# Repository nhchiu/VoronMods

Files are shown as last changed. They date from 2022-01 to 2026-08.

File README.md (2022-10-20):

# VoronMods



Collection of mods for Voron printers.

Feedbacks are welcome. @nhchiu#0363 on [Voron's Discord](https://discord.gg/voron) .

Support my work:



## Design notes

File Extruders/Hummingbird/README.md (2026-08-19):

# Hummingbird Extruder

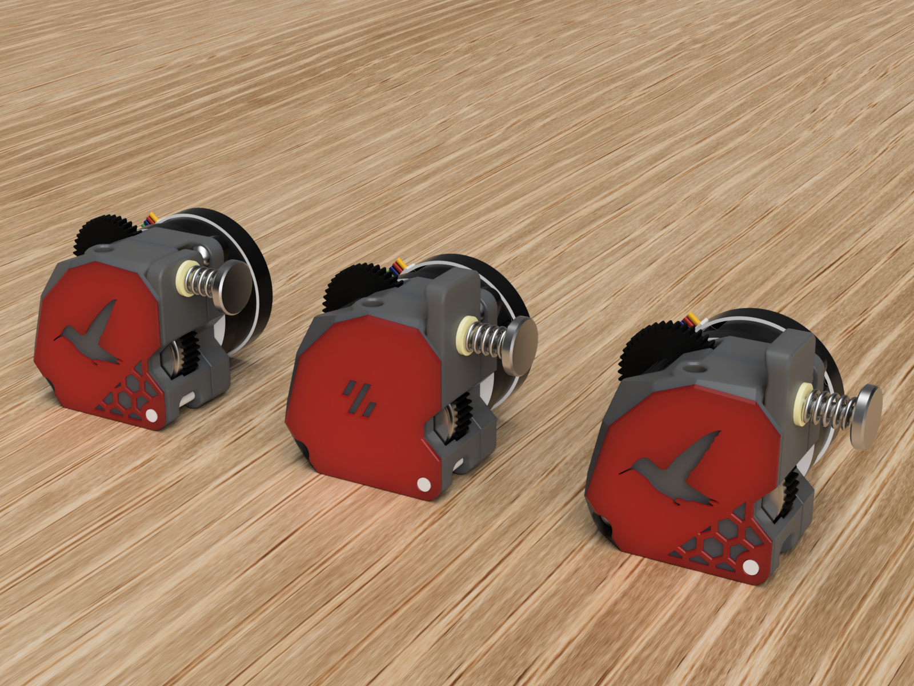
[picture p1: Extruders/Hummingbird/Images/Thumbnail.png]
Thumbnail


A compact extruder design that has the same form factor and mounting pattern as the [Bondtech LGX Lite](https://www.bondtech.se/product/lgx-lite-large-gears-extruder/).

It utilizes the large extrusion gears of [HGX-lite gear kit](https://www.aliexpress.com/item/1005004699143725.html) to accomplish high gear ratios and good filament grip.



> This page contains affiliate links. If you purchase products through these links, I may earn a small commission at no additional cost to you.
> This helps support the development and maintenance of my projects. Thank you for your support!

## BOM

- HGX Lite extruder gear kit ([AliExpress affiliate link](https://s.click.aliexpress.com/e/_DCabyeT))
  - Fasteners:
    - M3x8mm BHCS x 1
    - M3x12mm BHCS x 1
    - M3x20 SHCS x 1
    - Heat set inserts (M3 x D4.5 x H5) x 6
  - MR63ZZ bearings x 2
  - 3mm shaft (16mm length) x 2
  - 3mm shaft (24mm length) x 1
  - Large extrusion gear with pin bearing x 2
  - Reduction gear x 1
- NEMA14 36mm round pancake motor with 10T gear (Affiliate links: [Moons](https://s.click.aliexpress.com/e/_DlgBbDN) or [LDO](https://s.click.aliexpress.com/e/_Dm8FCDD))
- A short piece of PTFE tube (4mm OD, 2mm ID)

## Print Settings

Same as Voron spec. 4 perimeters, 40% infill. No support required.

To have the dual color effect as shown in the photo bellow, pause the print at 0.8mm height and change the filament color.

### Tip for bridging over the hexagonal grid

Use a height range modifier at 0.5-0.6 (mm) or add a cube modifier and place it at the height of the bridging, and force the bridging layer to print with only 2 perimeters.

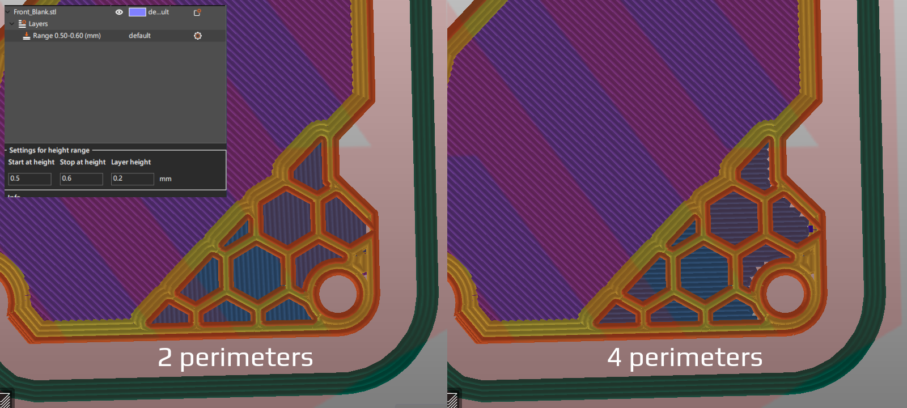
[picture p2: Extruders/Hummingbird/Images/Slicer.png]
Slicer


## Assembly

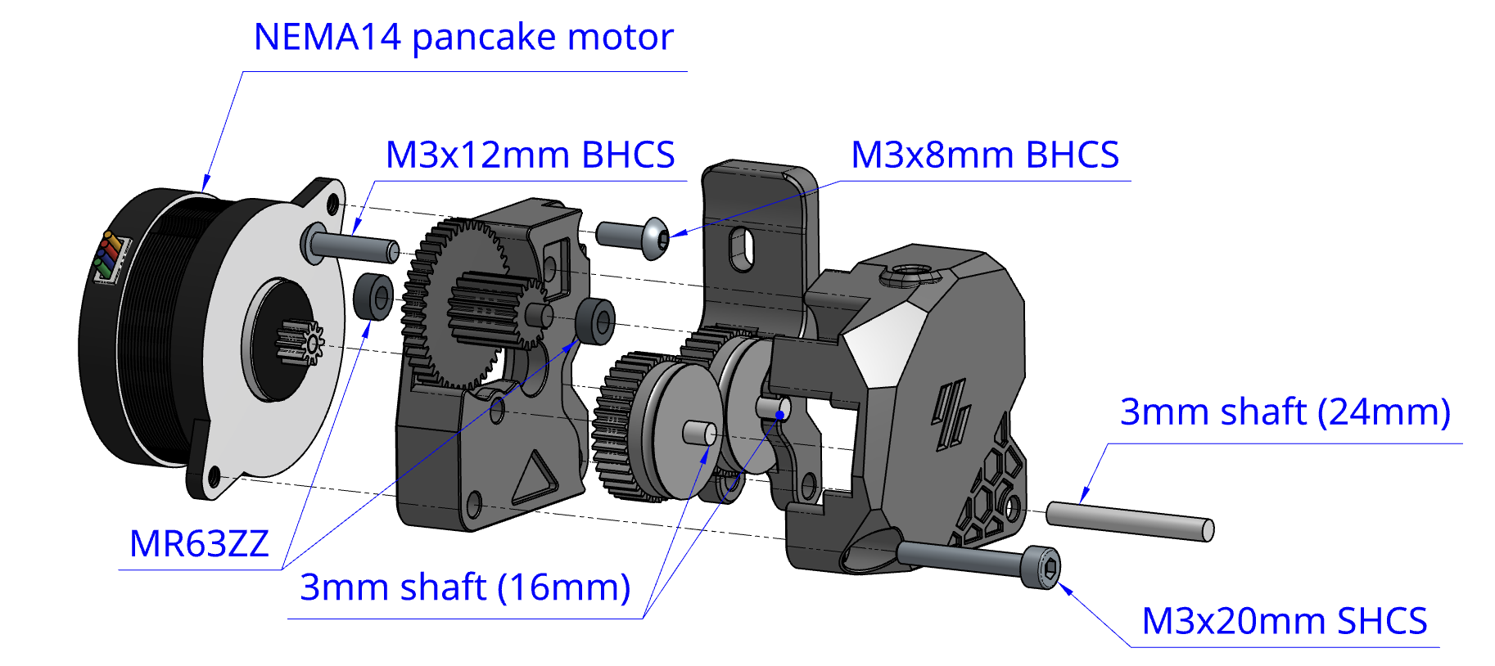
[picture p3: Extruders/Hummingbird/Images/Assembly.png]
Assembly


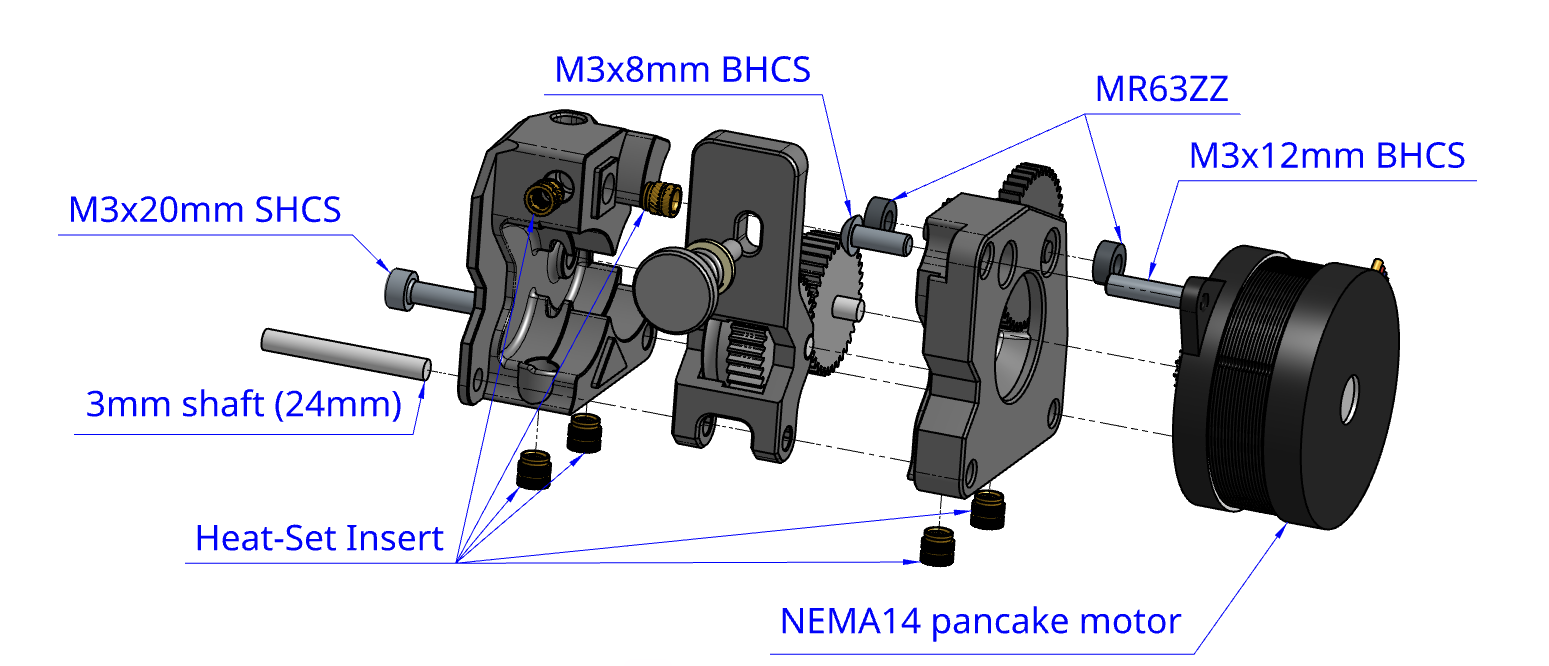
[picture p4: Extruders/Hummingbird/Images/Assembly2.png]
Assembly2


## Key Dimensions

All dimensions are in millimeters.

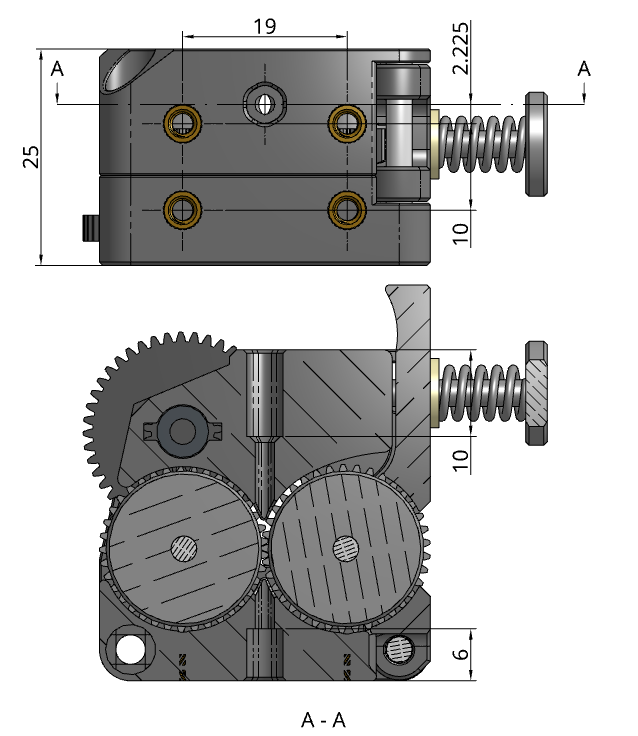
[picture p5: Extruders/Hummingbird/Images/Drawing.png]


## Firmware Settings

Only tested on [klipper firmware](https://www.klipper3d.org/):

```ini
[extruder]
rotation_distance: 53.494165  # Re-calibrate your own value
gear_ratio: 44:10, 37:17
```

## Photos

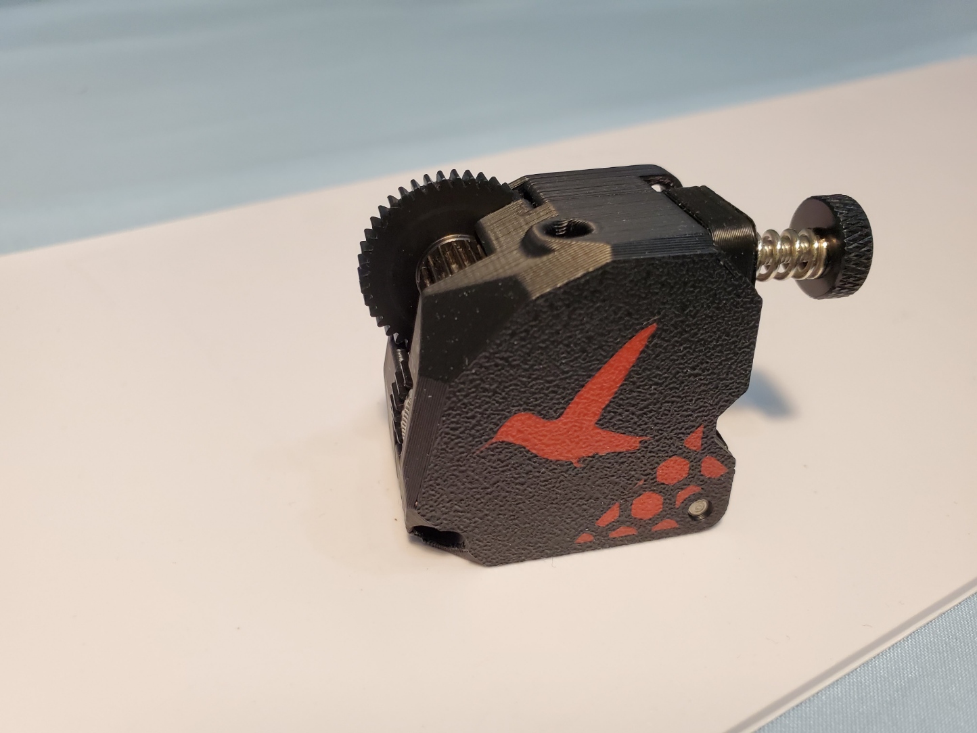
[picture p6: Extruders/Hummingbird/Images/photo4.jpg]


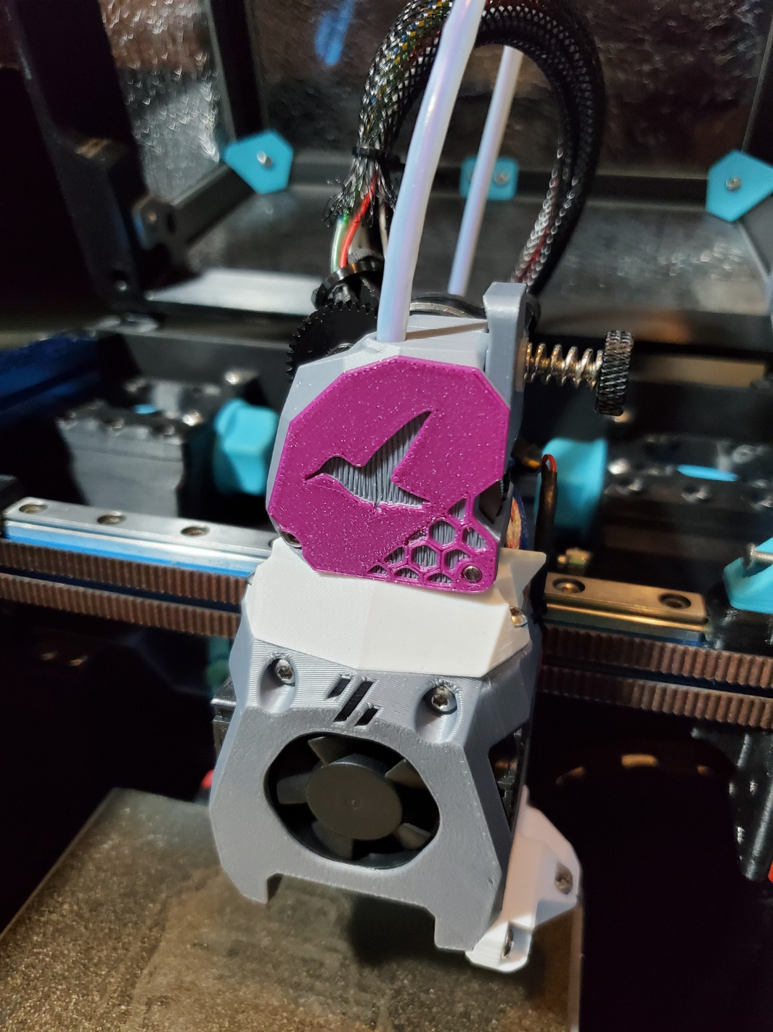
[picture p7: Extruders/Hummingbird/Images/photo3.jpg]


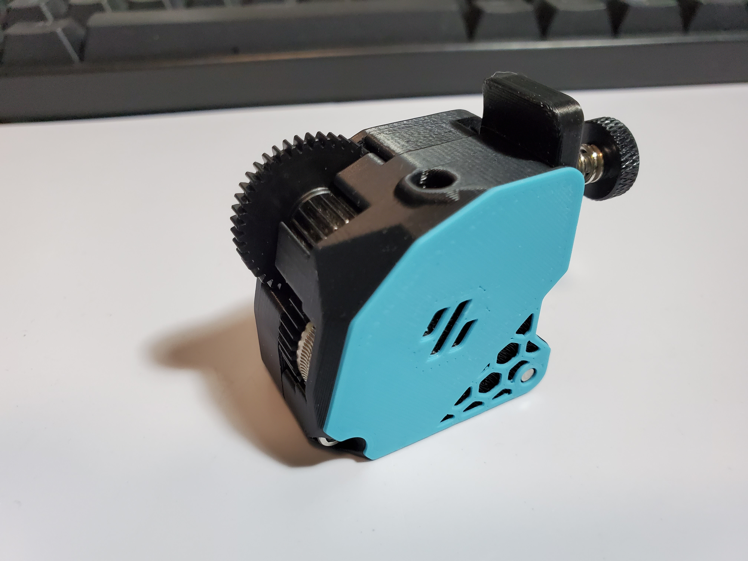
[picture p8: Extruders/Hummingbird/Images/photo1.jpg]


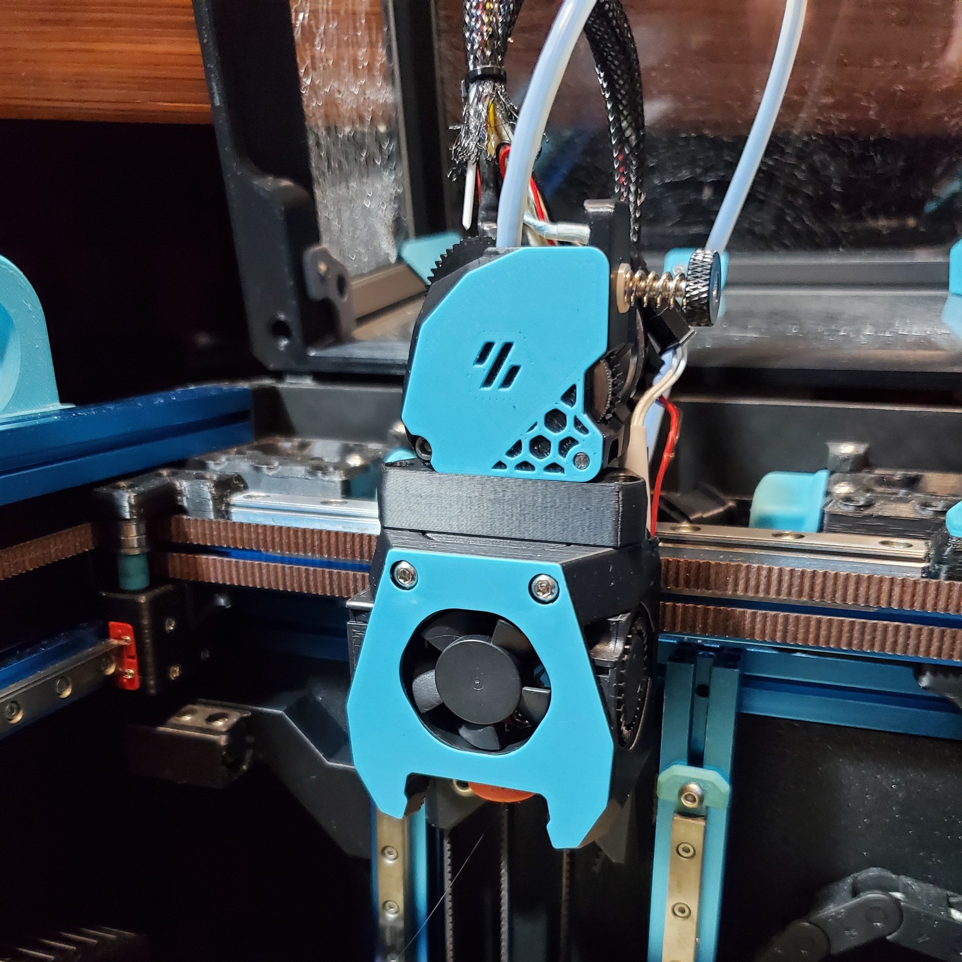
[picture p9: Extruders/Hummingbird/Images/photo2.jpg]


## Changelog

### 2024-05-08

- Removed the mockup gears in CAD to avoid confusion.

### 2023-06-28

- Added support for 3 kinds of PTFE tube retainers (4mm OD).

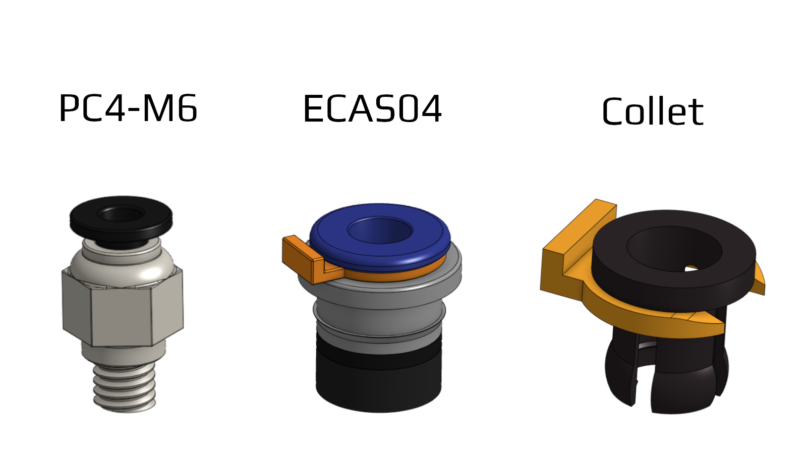
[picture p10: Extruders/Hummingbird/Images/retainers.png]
retainers
  

### 2023-05-02

- Increased the maximum distance that the idler gear can bite into the filament.
  This should prevent the filament from slipping due to the back pressure in the hotend.
- Made the idler arm thicker so it doesn't get bent over time.
- Added a multi-body STL (with MMU in the filename) for printing on a printer with MMU.

### 2023-04-01

- New hummingbird logo curtesy of #chewy2420 on Discord!
- Added a version without the hexagonal grid for easier print.
- New short idler arm for compact looking (you can still feed the filament by rotating the exposed large gear).
- Removed some plastic and tweaked some dimensions. **No part is compatible with previous versions!**

### 2023-01-13

- Initial release

## Credits and Related Projects

- [Bondtech LGX Lite - Large Gears eXtruder](https://www.bondtech.se/product/lgx-lite-large-gears-extruder/)
- [LGX lite Extruder on Printables](https://www.printables.com/model/282297-lgx-lite-extruder-fdm-case/comments) by [SIVIS](https://www.printables.com/social/263178-sivis)
- **Pixel Printing** on Discord for the name of the extruder

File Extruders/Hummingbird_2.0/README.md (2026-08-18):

# Hummingbird Extruder 2.0

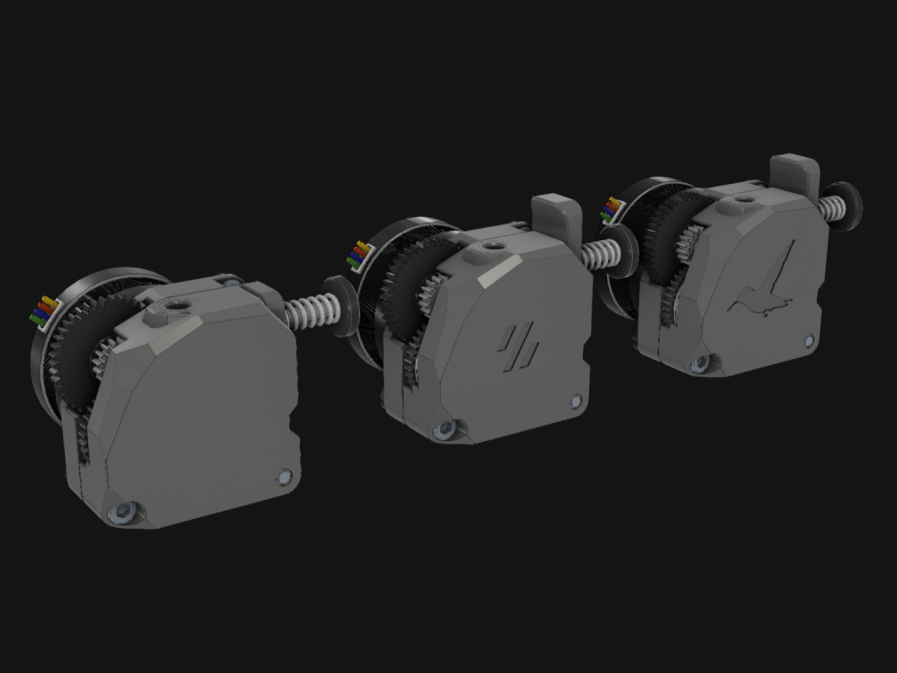
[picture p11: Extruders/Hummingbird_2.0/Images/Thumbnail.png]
Thumbnail


A compact extruder design that has the same form factor and mounting pattern as the [Bondtech LGX Lite](https://www.bondtech.se/product/lgx-lite-large-gears-extruder/).

Although it is named Hummingbird **2.0**, it's not a direct upgrade from the previous design.
There's not much you can reuse in the BOM.

It utilizes the large extrusion gears of [HGX-lite **2.0** Extruder](https://s.click.aliexpress.com/e/_Dmy9Crl) **(affiliate link)** to accomplish high gear ratios and good filament grip.

If you would like to support my work, the following platforms are available. Thank you!




> This page contains affiliate links. If you purchase products through these links, I may earn a small commission at no additional cost to you.
> This helps support the development and maintenance of my projects. Thank you for your support!



## BOM

- HGX Lite **2.0** extruder gear kit ([This](https://s.click.aliexpress.com/e/_Dmy9Crl) or [this](https://s.click.aliexpress.com/e/_Dn3gb6n)) **(Both are affiliate links)**.
  - MR63ZZ bearings x 6
  - 3mm shaft (16mm length) x 1
  - 3mm shaft (13mm length) x 1
  - Large extrusion gear x 2
  - Reduction gear x 1
- Fasteners:
  - M3x8mm BHCS x 1
  - M3x12mm BHCS x 1
  - M3x20 SHCS x 2
  - Heat set inserts (M3 x D5 x H4) x 4
- NEMA14 36mm round pancake motor with 10T gear
- A short piece of PTFE tube (4mm OD, 2mm ID)

## Print Settings

Same as Voron spec. 4 perimeters, 40% infill. No support required.

To have the dual color effect as shown in the photo bellow, pause the print at 0.8mm height and change the filament color.

## Assembly

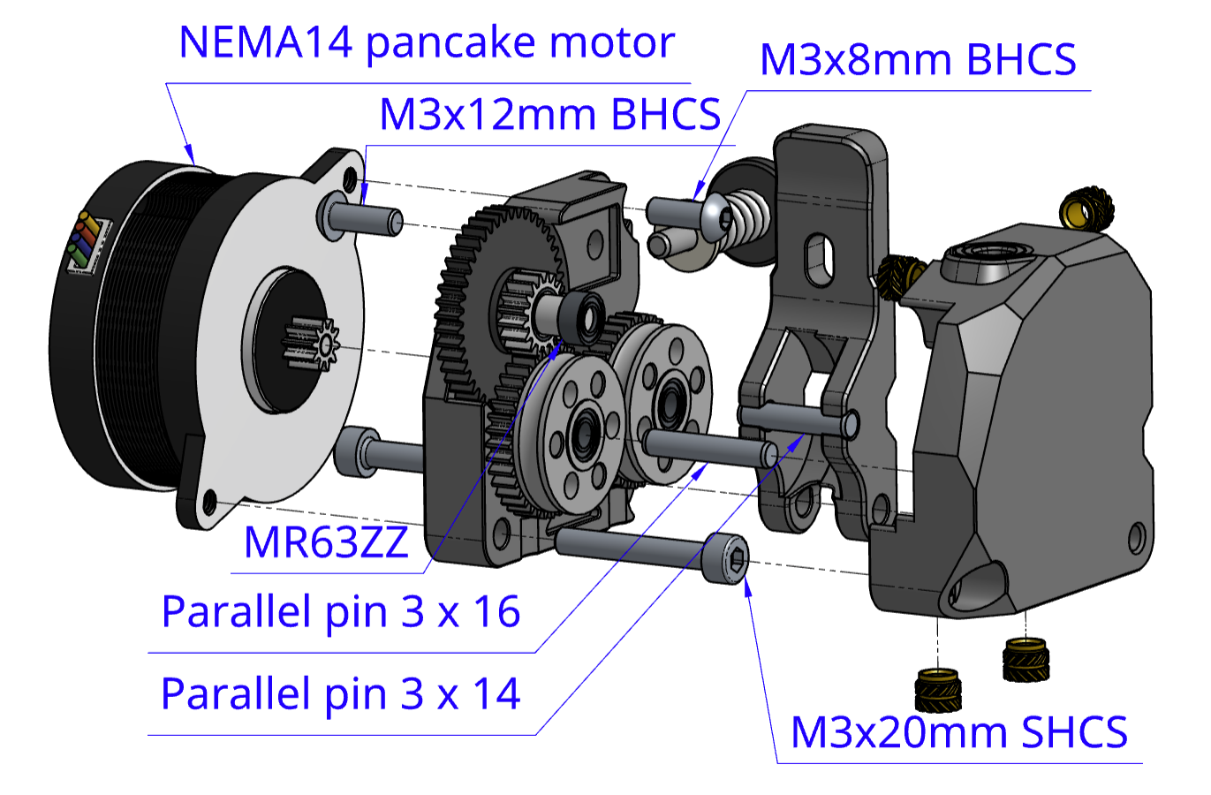
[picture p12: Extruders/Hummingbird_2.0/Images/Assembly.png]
Assembly


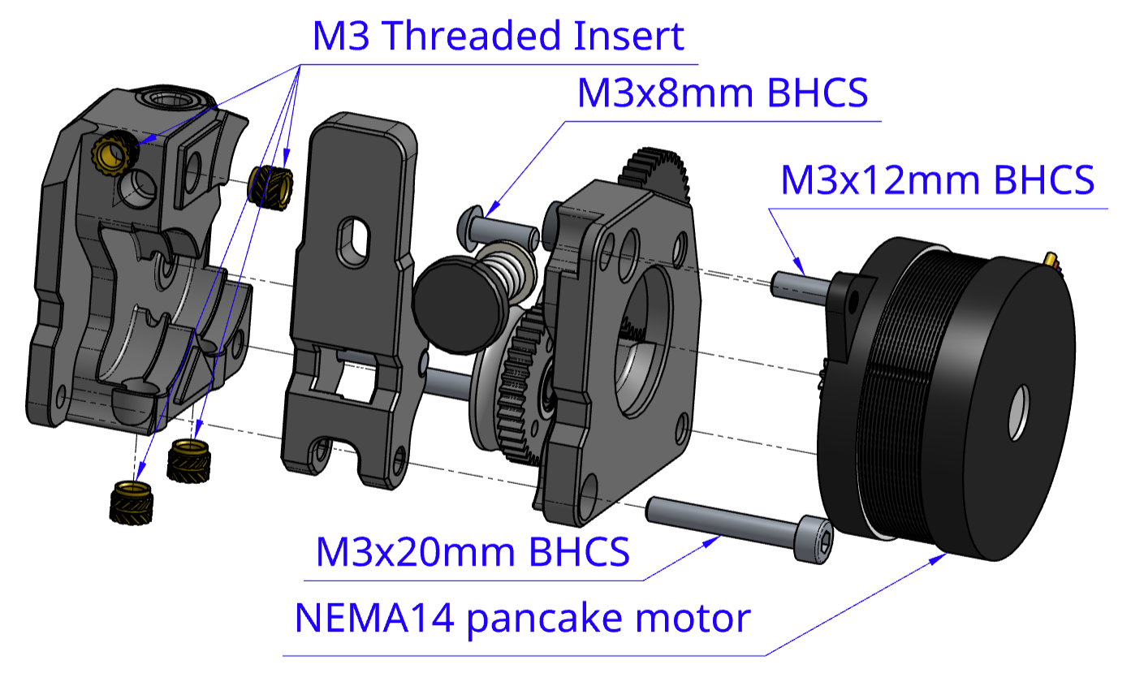
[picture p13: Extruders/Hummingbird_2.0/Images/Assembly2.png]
Assembly2


## Key Dimensions

All dimensions are in millimeters.

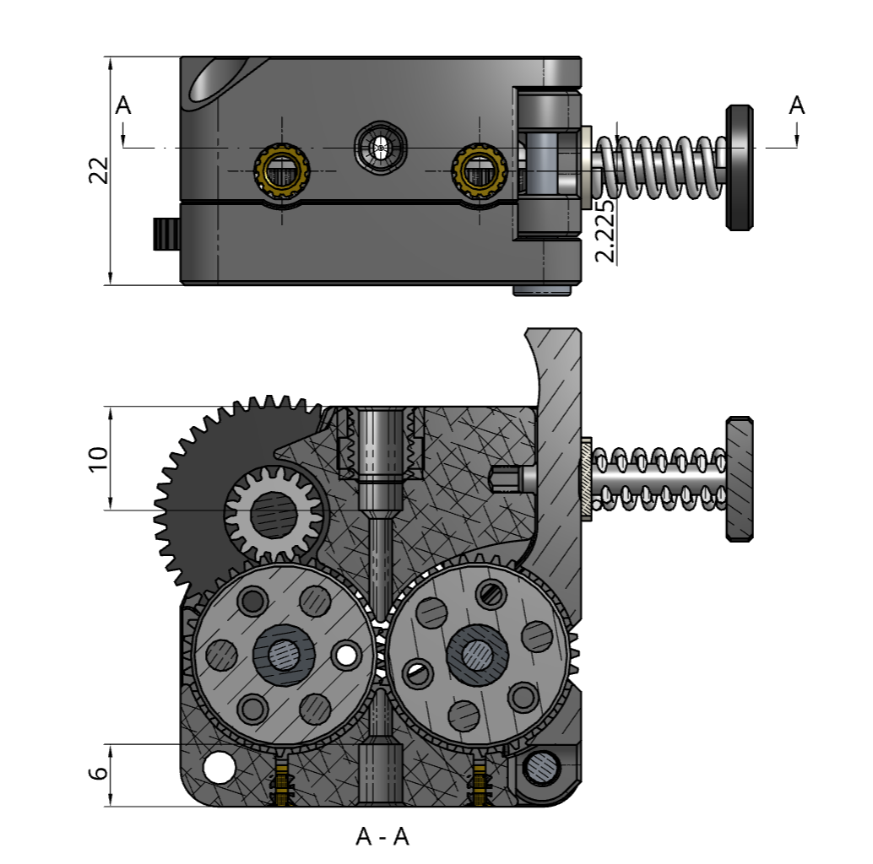
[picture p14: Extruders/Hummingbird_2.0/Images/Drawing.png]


## Firmware Settings

Only tested on [klipper firmware](https://www.klipper3d.org/):

```ini
[extruder]
rotation_distance: 53.494165  # Re-calibrate your own value
gear_ratio: 44:10, 37:17
```

## Photos

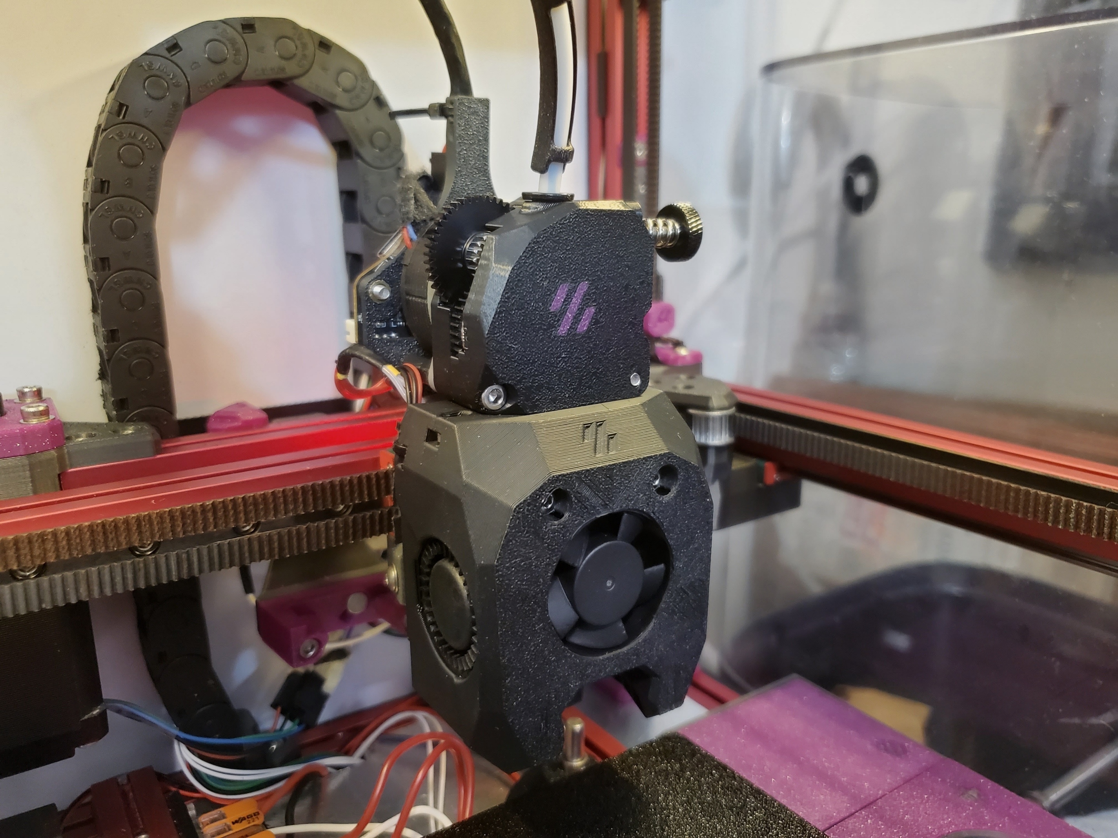
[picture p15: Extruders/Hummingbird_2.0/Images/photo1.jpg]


## Changelog

### 2026-08-18

- Initial release

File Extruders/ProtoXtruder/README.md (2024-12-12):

# ProtoXtruder

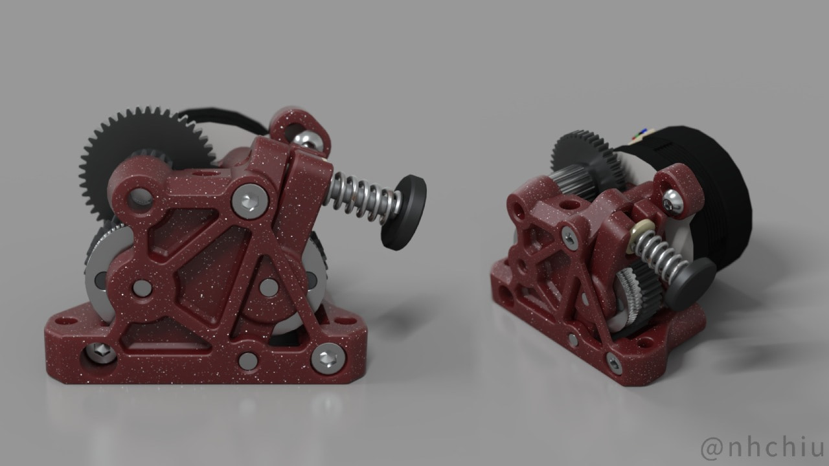
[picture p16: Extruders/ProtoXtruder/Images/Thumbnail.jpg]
Thumbnail


A extruder design that utilizes the large extrusion gears of [HGX-lite gear kit](https://www.aliexpress.com/item/1005004699143725.html)
and comes with the mounting pattern of the [Sherpa Mini Extruder](https://github.com/Annex-Engineering/Sherpa_Mini-Extruder).

There is also an **untested** version for [Bondtech LGX Lite](https://www.bondtech.se/product/lgx-lite-large-gears-extruder/) gears.

Refer to the following dimensions for compatibility with your printer.

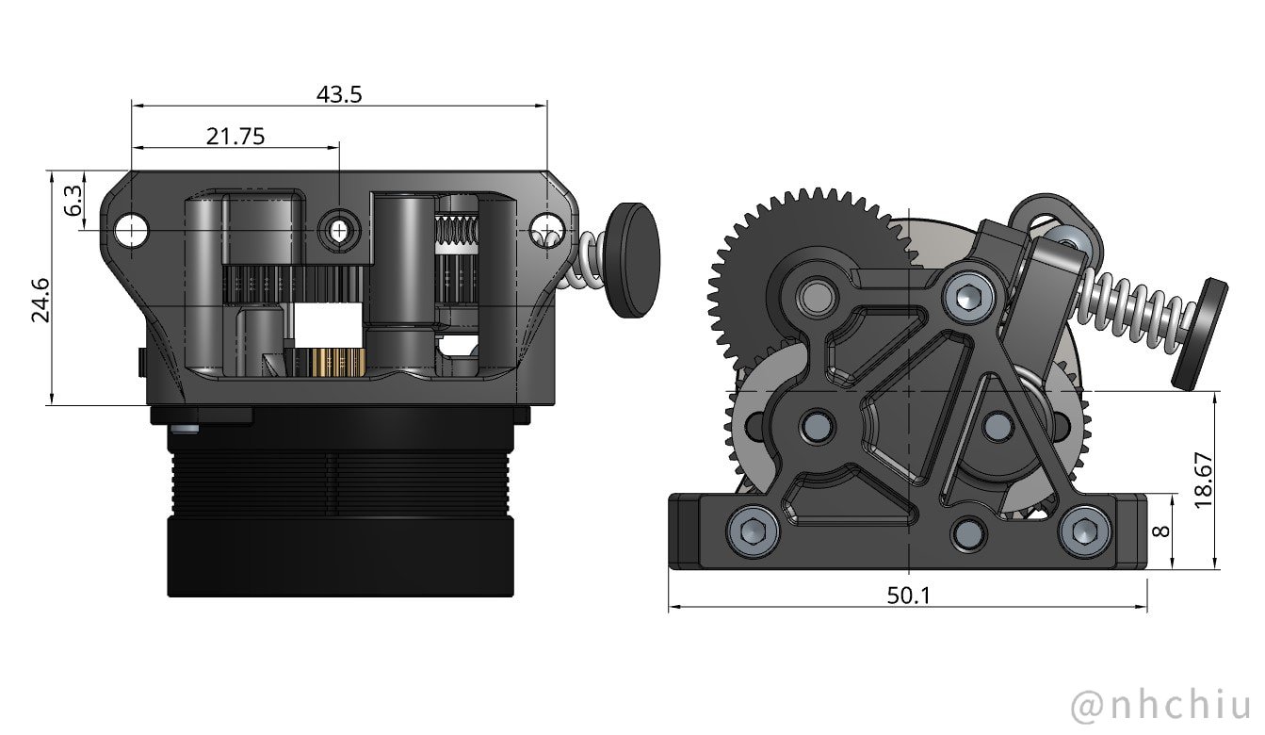
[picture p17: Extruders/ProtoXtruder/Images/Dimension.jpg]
Dimension




> This page contains affiliate links. If you purchase products through these links, I may earn a small commission at no additional cost to you.
> This helps support the development and maintenance of my projects. Thank you for your support!

## BOM

- HGX Lite extruder gear kit ([AliExpress affiliate link](https://s.click.aliexpress.com/e/_DCabyeT))
  ***Newer kits replaced each pin bearing with 2 MR63ZZ. Both versions will work. (But the gears have different ID so they are not interchangeable.)***
  - MR63ZZ bearings x 2
  - 3mm shaft (16mm length) x 2
  - 3mm shaft (24mm length) x 1
  - Large extrusion gear with pin bearing x 2
  - Reduction gear x 1
  - Fasteners (included in the gear kit):
    - M3x8mm BHCS x 1
    - M3x20mm SHCS x 3
    - Heat set inserts (M3 x D4.5 x H5) x 3
- NEMA14 36mm round pancake motor with 8T or 10T gear (Affiliate links: [Moons](https://s.click.aliexpress.com/e/_DlgBbDN) or [LDO](https://s.click.aliexpress.com/e/_Dm8FCDD))

## Print Settings

3 perimeters, 40% infill. ABS recommended.

All STLs are oriented in the printing orientation. No support required.

It will need some bridging.

## Assembly

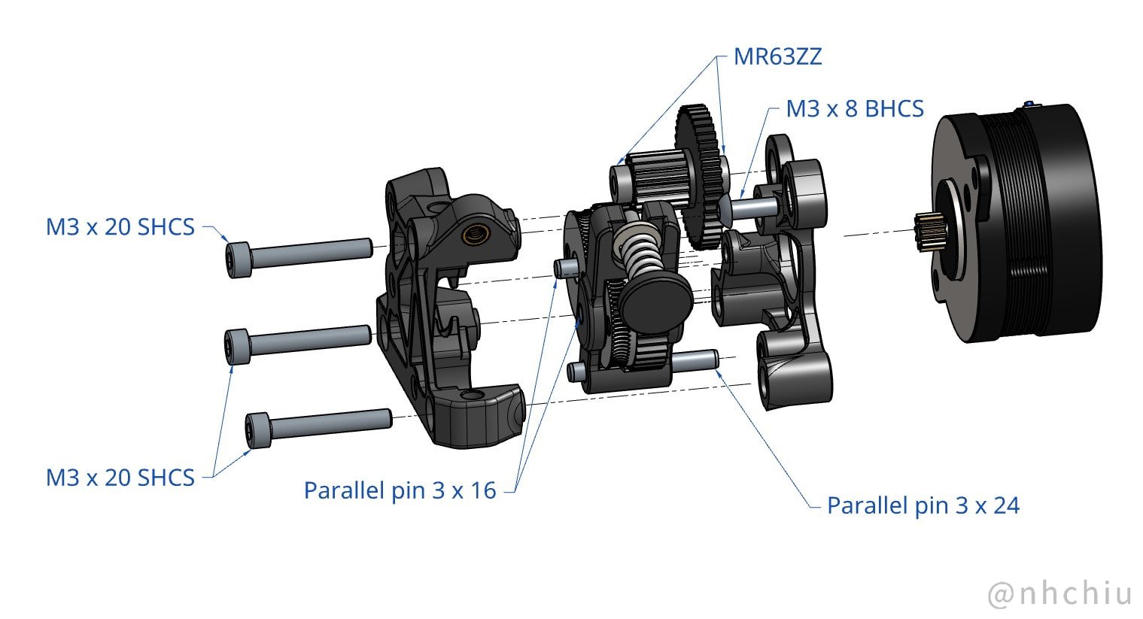
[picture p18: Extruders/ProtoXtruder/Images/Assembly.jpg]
Assembly


\* Remove the bottom half of the ECAS04 before inserting. (the black parts in plastic/rubber)

https://user-images.githubusercontent.com/14959712/228478235-7f9f1ea8-db8a-41ff-84bd-ff1c1cee3275.mp4

## Firmware Settings

For [klipper firmware](https://www.klipper3d.org/):

```ini
[extruder]
rotation_distance: 53.494165  # Re-calibrate your own value
gear_ratio: 44:10, 37:17
```

**You have to invert the `dir_pin` of the extruder if you were using a BMG gear kit.**

## Photo

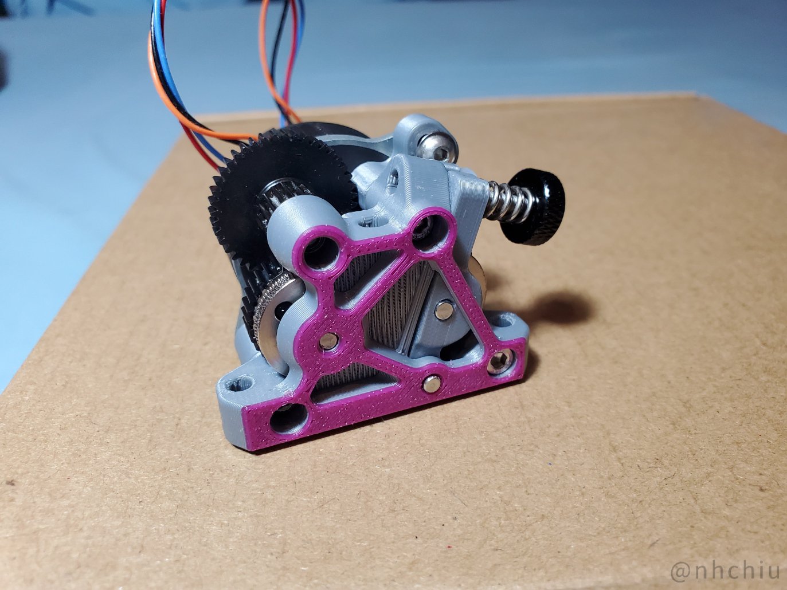
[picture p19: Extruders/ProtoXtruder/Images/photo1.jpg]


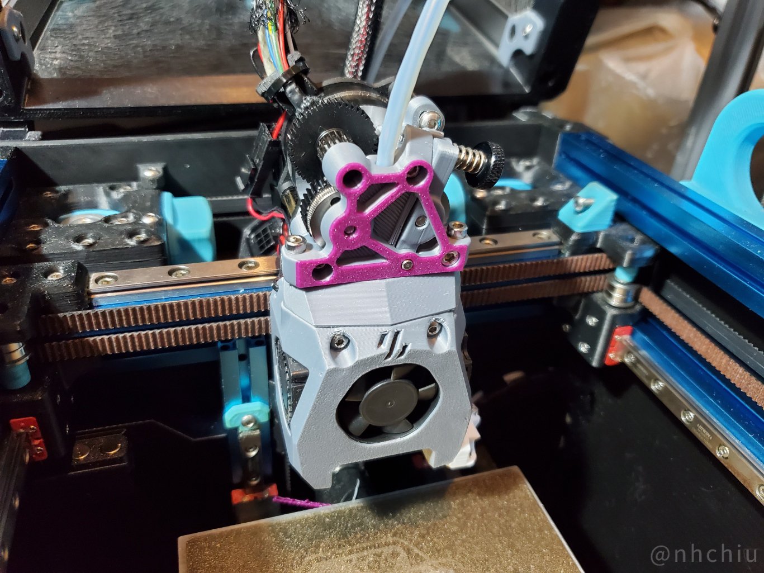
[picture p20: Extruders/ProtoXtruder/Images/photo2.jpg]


## Changelog

### 2024-12-12

Bugfix update.

- Thicker idler arm to prevent it being bent over time. Hopefully fixes [#20](https://github.com/nhchiu/VoronMods/issues/20).
- The update at 2024-08-01 might cause the idler arm being bottomed out by tension and
  still not providing enough pressure on the filament. Slightly shortened the distance between the
  dual drive gears to address this issue.

### 2024-10-21

- Updated the collet cutout for better tube retaining and filament loading.
  No changes were made to other variants.
  Thanks to @MartijnGevaert for the suggestion.

### 2024-08-01

- Made better measurements of the HGX gears and slightly tweaked some dimensions accordingly.
- Some overall cleanups and aesthetic adjustments. Now the printed parts use roughly 10% less plastic.

### 2023-07-02

- Increase the maximum compression on the filament for better gripping.
- Fix the hole size of the idler shaft so it doesn't slip out during print.
- Variants for 3 types of Bowden tube retainers.

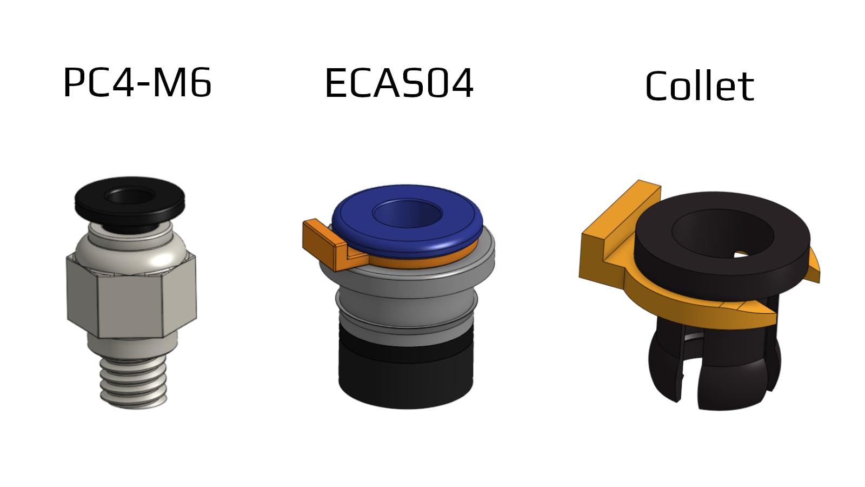
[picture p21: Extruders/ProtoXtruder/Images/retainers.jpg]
retainers
  
- Replaced the M3 x 16 screw to M3 x 20 to make space for the Bowden tube retainers.

### 2023-03-29

- Initial release

## Credits

- [Sherpa Mini Extruder](https://github.com/Annex-Engineering/Sherpa_Mini-Extruder) by [Annex Engineering](https://github.com/Annex-Engineering)

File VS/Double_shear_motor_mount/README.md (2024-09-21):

# Voron Switchwire Double Shear Motor Mount

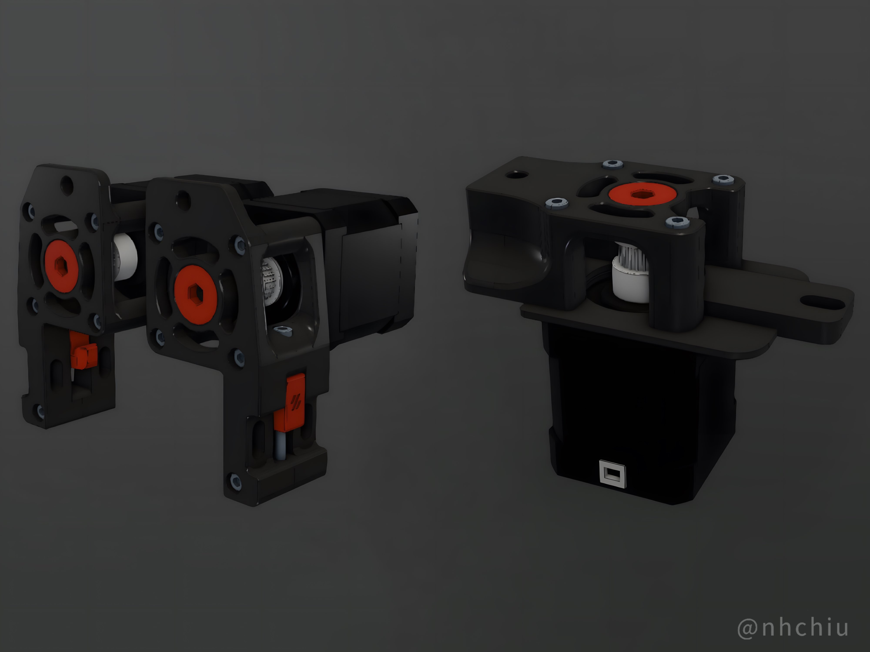
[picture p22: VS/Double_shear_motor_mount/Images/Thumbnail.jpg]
Thumbnail




This mod adds another bearing on the motor mount to support the other end of the motor shaft.
It reduces the bending effect on the shaft caused by the tension of the timing belt.
In theory it can make the motor runs smoother under high belt tension and most likely increase its lifespan too.

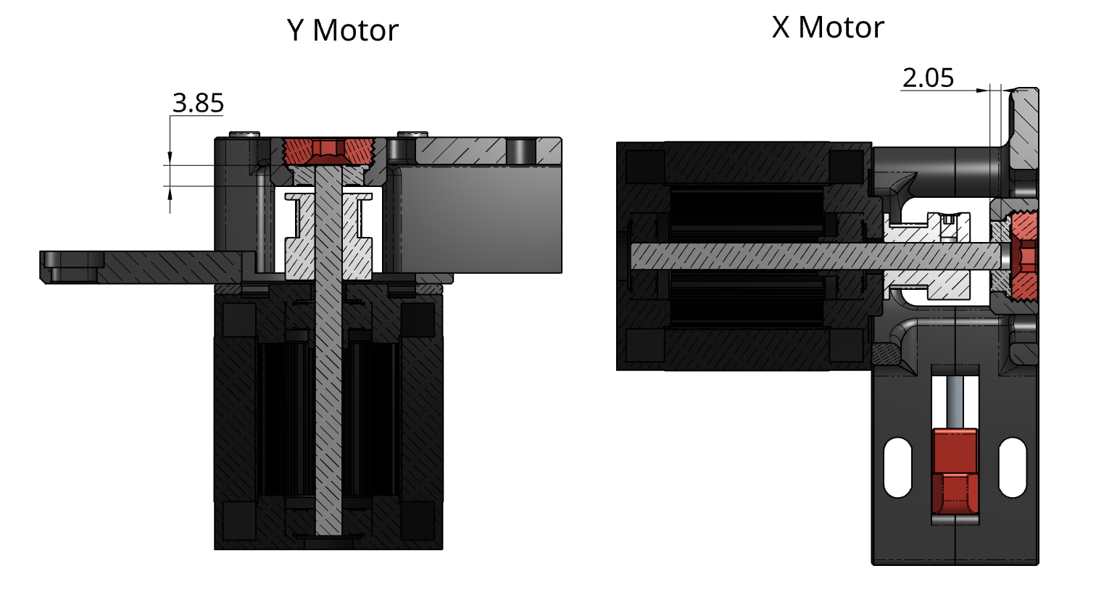
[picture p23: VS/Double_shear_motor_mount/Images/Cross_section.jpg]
cross_section


**All dimensions are designed to fit the stock Switchwire motors (24mm long shaft). If your motor has longer or shorter shaft, please check if it fits before proceeding.**
With the stock motor shaft length, the shaft can't reach through the full height of the bearing on X/Z motor mounts. But it should more or less still be helpful to hold the floating end of the shaft.

If you like my design, please consider supporting my work through the following platforms. Thank you!




## Features

- Double shear mount.
- Added indexing features between mating parts.
- Some tweaks on the XZ motor mounts ported from [SW More Robust XZ Belt Paths by yenda](https://github.com/VoronDesign/VoronUsers/tree/main/printer_mods/yenda/vsw_more_robust_belt_paths):
  - Added an additional screw at the bottom. The two halves of the motor mount tend to slightly split up and show a gap there so this screw helps holding them together.
  - An additional screw hole to help fixing the motor mount to the Z(vertical) extrusion. **Use this screw with care. Don't rely on this screw to force the motor mount to fit to the vertical extrusion. Make sure the frame is square and the motor mount is properly installed first, then install this screw lightly just as an extra reinforcement.**

    > Quote from yenda's mod:
    >
    > It has been noticed by people helping within Voron community with Switchwire builds on regular basis,
    > that the uppermost screw supposed to fix the stepper mounts to the vertical extrusions might actually cause issues if the frame is not perfectly square.
    > Please make sure your printer has its frame fully square and proceed at your discretion -- use of the uppermost screw is solely optional in any case. (Credits for this observation go to Hymness1 on Voron Discord).

## BOM

Only additional parts from the stock Switchwire design are listed here.

- X/Z motor mount (per side)
  - F695 bearing x 1 (either ZZ or RS type would work)
  - M3xD5xH4 threaded insert x 1
  - M3x25 SHCS x 1
  - M5x10 BHCS x 1 and M5 T-nut for 3030 extrusions x 1 (Optional. For attaching to the Z extrusion)
- Y motor mount
  - F695 bearing x 1 (either ZZ or RS type would work)
- Extra tools
  - 5mm Allen key / hex driver (Just for tightening the bearing retainer. Printed hex key might work too.)

## Print Settings

Same as Voron spec. 0.2mm layer height, 4 perimeters, 40% infill, 5 solid top/bottom layers.

All STLs are oriented in the printing orientation. No support required.

## Assembly

Please refer to [Assembly_Manual.pdf](./Assembly_Manual.pdf).

## Photos

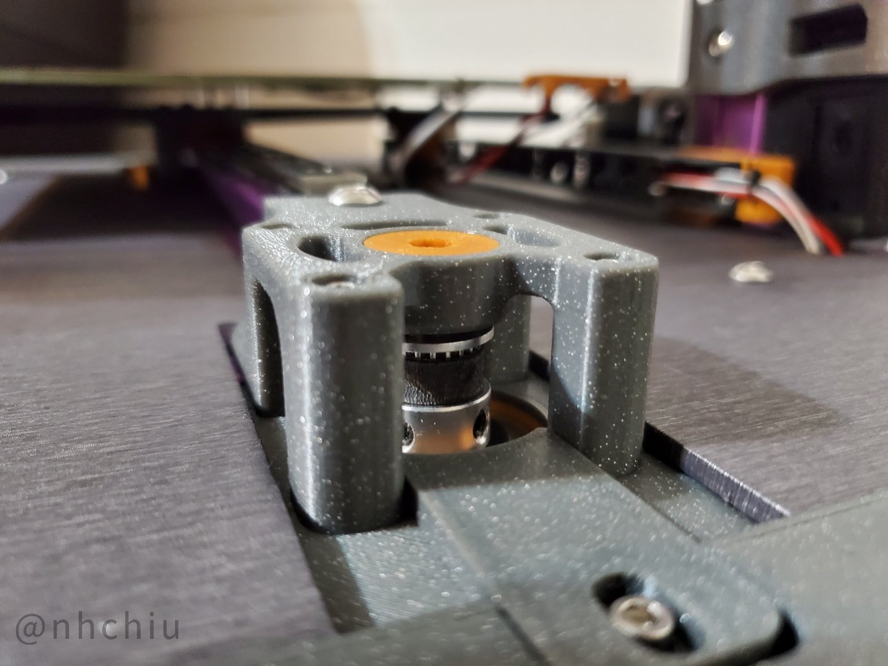
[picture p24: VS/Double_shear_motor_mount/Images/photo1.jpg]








## Changelog

### 2024-09-21

- Initial release

## Credits

- [Voron Switchwire](https://github.com/VoronDesign/Voron-Switchwire)
- [SW More Robust XZ Belt Paths by yenda](https://github.com/VoronDesign/VoronUsers/tree/main/printer_mods/yenda/vsw_more_robust_belt_paths)

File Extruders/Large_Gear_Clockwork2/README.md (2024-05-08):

# Large Gear Clockwork2

Thumbnail

As title, it's basically [Voron Clockwork2](https://github.com/VoronDesign/Voron-Stealthburner/tree/main/STLs/Clockwork2) utilizing the large extrusion gears of [HGX-lite gear kit](https://www.aliexpress.com/item/1005004699143725.html) or [Bondtech LGX Lite eXtruder](https://www.bondtech.se/product/lgx-lite-large-gears-extruder/) to accomplish high gear ratios and good filament grip.

**If you are going to use a toolhead board, this would probably be only compatible with the 2-piece version of the [Stealthburner toolhead board](https://github.com/VoronDesign/Voron-Hardware/tree/master/Stealthburner_Toolhead_PCB) (mount it directly without the PCB spacer). The standard version will interfere with the gear below. *Check your own toolhead board / CAN board before use!***



## BOM

- HGX Lite extruder gear kit ([https://www.aliexpress.com/item/1005004699143725.html](https://www.aliexpress.com/item/1005004699143725.html))
  - MR63ZZ bearings x 2
  - 3mm shaft (16mm length) x 2
  - 3mm shaft (24mm length) x 1
  - Large extrusion gear with pin bearing x 2
  - Reduction gear x 1
- NEMA14 36mm round pancake motor with 10T gear
- Fasteners:
  - M2x10 self-tapping screw x 1
  - M3x6  BHCS x 1
  - M3x8  SHCS x 2
  - M3x16 SHCS x 1
  - M3x20 SHCS x 1
  - M3x25 SHCS x 4
  - M3xD5xH4 threaded inserts x 13 or 14 (depending on the mounting holes of your drag chain)

**Note: Use the threaded inserts in the Voron BOM. The inserts included in the HGX Lite gear kit has a different dimension!**

## Print Settings

Same as Voron spec. 4 perimeters, 40% infill.

All STLs are oriented in the printing orientation. No support required.

## Assembly

Please refer to [Assembly.pdf](./Assembly.pdf).

## Firmware Settings

For [klipper firmware](https://www.klipper3d.org/):

```ini
[extruder]
rotation_distance: 53.494165  # Re-calibrate your own value
gear_ratio: 44:10, 37:17
```

**You have to invert the `dir_pin` of the extruder if you were using a BMG gear kit.**

## Photo









## Changelog

### 2024-05-08

- Removed the mockup gears in CAD to avoid confusion.

### 2023-07-10

- Increased the maximum squish on the filament.
- Tweaked some dimensions here and there.
- Included a variant using LGX-lite gears.

### 2023-02-20

- Initial release

## Credits

- [Voron Stealthburner and Clockwork2](https://github.com/VoronDesign/Voron-Stealthburner)
- [Bondtech LGX Lite eXtruder](https://www.bondtech.se/product/lgx-lite-large-gears-extruder/)

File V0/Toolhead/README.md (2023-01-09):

# Mini Stealthdort

Thumbnail

Yet another versatile toolhead design for Voron-0.

## Features

- Shorter distance between the extruder and the hotend.
- Light-weight printed parts.
- The extruder will be mounted 4mm lower, so the tube is less likely to rub on the top-hat.
- Built in cut-out for [Klicky probe](https://github.com/jlas1/Klicky-Probe/tree/main/Printers/Voron/v0) and [ZeroClick](https://github.com/zruncho3d/ZeroClick) (use the provided probe STLs in this repo).
- Redesigned part cooling fan duct.
- Similar mounting style as [Mini AfterSherpa](https://github.com/PrintersForAnts/Mini-AfterSherpa)
  The mounting holes and dimensions are mostly compatible with Mini AfterSherpa but the top surface is 4mm lower

  

## BOM

- M3 Heatset insert x 2 (for the extruder mount)
- **M3x30mm** x 2 (for mounting to the carriage)
- 3010 blower fans for part cooling
- 3007 or 3010 axial fan for hotend cooling (depending on the hotend)

Optional:

- One M3 heatset insert for klicky probe mount
- M2x8mm screw for ZeroClick (Or use the M2 self-tapping screw with Voron BOM and trim down 2mm)
- M3x40mm x 2 (for mounting ADXL345)

## Supported Hardware

Choose the supported extruder and hotend listed bellow and print the corresponding STL files.

### Extruder

extruder

| Extruder | Printed parts |
| --- | --- |
| [Vorxtrudort](https://github.com/nhchiu/VoronMods/tree/main/Extruder) | `Cowling.stl` |
| [Sherpa Mini](https://github.com/Annex-Engineering/Sherpa_Mini-Extruder) | `Cowling.stl` |
| [Sherpa Micro](https://github.com/Annex-Engineering/Sherpa_Micro-Extruder) | `Cowling.stl` and `Sherpa_micro_adapter.stl`  |
| [Sailfin](https://github.com/CroXY3D/Sailfin-Extruder) or [Sharkfin](https://github.com/KayosMaker/Sailfin-Extruder/tree/main/Usermods/KayosMaker/Sharkfin) (with Sherpa mount variant) | `Cowling.stl` and `Sailfin_spacer.stl` |
| [Orbiter V1.5](https://orbiterprojects.com/orbiter-1-5) | `Cowling.stl` and `Orbiter_V1.5_adapter.stl`  |
| [Orbiter V2.0](https://orbiterprojects.com/orbiter-v2-0/) | `Orbiter_V2_cowling.stl` |
| [LGX Lite](https://www.bondtech.se/product/lgx-lite-large-gears-extruder/) | `Cowling.stl` and `LGX_Lite_adapter.stl` |
| [Vz-Hextrudort](https://github.com/VzBoT3D/Vz-HextrudORT) | `Cowling.stl` and `Vz-Hextrudort_adapter.stl` |

### Hotend

hotend

| Hotend | Supported Hotend Fan | Printed Part |
| --- | --- | --- |
| Phaetus Dragon | 3007 | `Dragon-Mount.stl` |
| Phaetus Dragonfly BMO | 3007 | `Dragonfly-BMO-Mount.stl` |
| Slice Engineering Mosquito | 3010 & 3007 | `Mosquito-Mount.stl` |
| E3D Revo Voron | 3010 & 3007 | `Revo-Voron-Mount.stl` |
| Mellow NF-Zone | 3010 & 3007 | `NF-Zone-Mount.stl` |

## Assembly

assembly

## ADXL345 Mount

Print out `ADXL345_Mount.stl` and mount the ADXL345 module to it with 2 M2 self-tapping screws and 2 [printed washer (from Stealthburner)](https://github.com/VoronDesign/Voron-Stealthburner/blob/main/STLs/Stealthburner/ADXL345_Mounts/sb_adxl_washer_x2.stl).

Use 2 M3x40mm screws to mount it on the toolhead for calibrating input shaper.

ADXL

## Photo



## Changelog

### 2023-01-09

- Added supported extruder: Sherpa Micro, Orbiter V2.0, LGX Lite, Vz-Hextrudort
- Added supported hotend: Mellow NF-Zone
- Modular design for hotend and extruder so switching hotend is much easier
- Tweaked the low-poly design
- Filled up the gap between the klicky probe mount and the heatset insert

### 2022-08-04

- Added untested support for Sailfin / Sharkfin extruder and Orbiter V1.5

### 2022-07-30

- Revised the fan duct
- Moved the zip tie slot higher so it clears the X carriage
- Tweaked some faces and removed most of the fillets

### 2022-07-16

- Added E3D Revo Voron support (not tested yet)

### 2022-07-10

- Initial release

## Credits and Related Projects

- [Voron-0 and Mini AfterBurner](https://github.com/VoronDesign/Voron-0) by VoronDesign
- [Mini AfterSherpa](https://github.com/PrintersForAnts/Mini-AfterSherpa)
- [Mini After-LGX-Lite](https://github.com/VoronDesign/VoronUsers/tree/master/printer_mods/Bondtech/Mini-After-LGX-Lite)
- [MiniAfterHybrid](https://github.com/camerony/VoronCustom/tree/main/v0.1_MiniAfterHybrid)
- [Apogee Tool Head](https://orbiterprojects.com/ender-3-v2/)
- [Sherpa Mini Extruder](https://github.com/Annex-Engineering/Sherpa_Mini-Extruder)
- [Sailfin Extruder](https://github.com/CroXY3D/Sailfin-Extruder)
- [Sharkfin Extruder](https://github.com/KayosMaker/Sailfin-Extruder/tree/main/Usermods/KayosMaker/Sharkfin)
- [Orbiter Projects](https://orbiterprojects.com)
- [Klicky Probe](https://github.com/jlas1/Klicky-Probe)
- [ZeroClick](https://github.com/zruncho3d/ZeroClick)

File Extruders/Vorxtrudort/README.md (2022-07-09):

# Vorxtrudort (HextrudORT for Voron)

Thumbnail

Design is based on the compact and lightweight [HextrudORT](https://miragec79.github.io/HextrudORT/).

HextrudORT is designed to be integrated with the X carriage and the hotend to make a compact toolhead, which is not directly compatable with modular toolhead design.

The major changes of Vorxtrudort are:

1. Stand-alone extruder with different mounting options.
2. Reduce printing support material.
3. Use heatset inserts instead of hex nuts.

I don't have a scale. If anyone would like to do a weight comparison with other extruder, please share it on Voron Discord.

## BOM

- Bondtech BMG internals
- NEMA14 36mm round pancake motor with 10T gear
- A short peice of PTFE tube (4mm OD, 2mm ID)
- M3 Heatset insearts (M3xD5xH4) x 4
- M3 BHCS or SHCS:
  - 8mm x 5
  - 16mm x 1
  - 20mm x 1
  - 25mm x 1
- M2 x 10mm Self Tapping Screw x 1

## Print Settings

Same as Voron spec. 4 perimeters, 40% infill.

No support. There are built-in support in the STL.

## File Naming

There are several variations. For the coresponding files they are named as follows:

`Part_Name_[Mounting_Pattern]_[PTFE_Inlet]`

Available mounting pattern: `SherpaMini` or `OrbiterV2`

PTFE inlet: `FrictionFit` or `Collet`





## Assembly









## Photo



## Changelog

### 2022-07-09

- Initial release

## Credits and Related Projects

- [HextrudORT](https://miragec79.github.io/HextrudORT/) by [MirageC79](https://github.com/MirageC79)
- [Sherpa Mini Extruder](https://github.com/Annex-Engineering/Sherpa_Mini-Extruder) by [Annex Engineering](https://github.com/Annex-Engineering)
- [Orbiter Projects](https://orbiterprojects.com/) by Róbert Lőrincz

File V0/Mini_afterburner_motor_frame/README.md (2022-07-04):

# Motor Frame Mod for Mini Afterburner

Motor frame mod ([link to the original file](https://github.com/VoronDesign/Voron-0/blob/Voron0.1/STLs/Toolheads/Mini_Afterburner/Motor_Frame_x1.stl)) for mini-afterburner.
This is my attempt to solve the wood grain / issue-6 print quality problem, and also make it less prone to some other issues.

Changes

The following changes are made:

1. Slotted screw hole on one side so the motor can be slightly moved to adjust for better gear meshing.
2. Strengthen the top of the part so the frame doesn't get bent easily if the top two screws are over-tightened.
3. Shrinked this hole for the screw to thread into platic (Refer to the assembly instruction for more info).
4. Removed the two holes for M2 self-tapping screws.

## BOM

The printed part, and replace one M3x35 (for the guidler) with M3x30.

## Assembly Instruction

I tried slightly changing the way mini-AB is assemled.
Hope it is easier and doesn't run into issues.

1. Put the BMG gears and mid body together without the M3 screws.

   
   

2. Put the MR85 bearing and the motor frame on.

   Make sure the shaft doesn't protude the back of the moter frame.

   
   

3. Fasten three M3x30 screws.

   Note the one going through the guidler screws directly into plastic and doesn't extend beyond the motor frame.

   **They should be just slightly tight enough that hold the parts together. No extra torque!**

   
   

4. Mount the motor. First fasten the right side and leave the left screw a bit loose.

   There should be some space for the motor to move up and down.

   The gears are blocked inside so you cannot test the gear meshing like assembling Clockwork.

   First pull the motor all the way down so the gears should be tight against each other, and then back up just the tiniest bit you can move.

   

5. Finally, put two M3x35 screws on and mount to the X carriage.

   
   

## Changelog

### 2022-07-04

- Initial release

## Credit

@Nemgrea and the Voron Design crews for the mini-AB design.

If you tried this, feedbacks are welcome through Voron Discord, @nhchiu#0363.

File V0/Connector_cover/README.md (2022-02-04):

# Connector Cover for Voron 0.1

Thumbnail
Front_and_Side_View

I could not get the wires tidy for the mini-AB. So I made a cover like the AfterBurner does.

Print with the Voron standard settings. No support required.

It should be a drop-in replacement for the [Strain_Relief_Body_x1.STL](https://github.com/VoronDesign/Voron-0/blob/Voron0.1/STLs/Toolheads/Mini_Afterburner/Strain_Relief_Body_x1.STL).

## Photos

Messy
Cover
Back
Front

## Changelog

### 2022-02-04

- Initial release

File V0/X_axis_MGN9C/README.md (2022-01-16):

# X Axis MGN9C Mod

Thumbnail

## BOM

### Fasteners

- 7 x M3x8 SHCS
- 7 x M3 Hex Nut
- 4 x M3x6 BHCS

### Motion

- 1 x MGN9 Rail - 150mm
- 1 x MGN9C Carriage

### Printed Parts

All the parts in the STLs folder is oriented and named with the Voron convension.

Print with the official suggested settings (4 perimeters, 0.4mm line width, 40% infill).

## Components

1. X Carriage

   X_Carriage

   It is made compatible with openbuild M3 T-nuts (10mm width) to hold the belts.

2. A/B Motor Mounts

   Motor_Mount

   Added some clearance so no colision at Y max.

3. M3 Nut Spacers (optional)

   M3_Nut_Spacers

   Keep the M3 hex nuts align with the MGN9 rail.

   Slide into the extrusion slot with the nuts facing **upwards**.

   (It might be too thick for MakerBeam extrusions.)

<!--

## Instructions

## Photos-->

## Changelog

### 2022-01-17

- Initial release

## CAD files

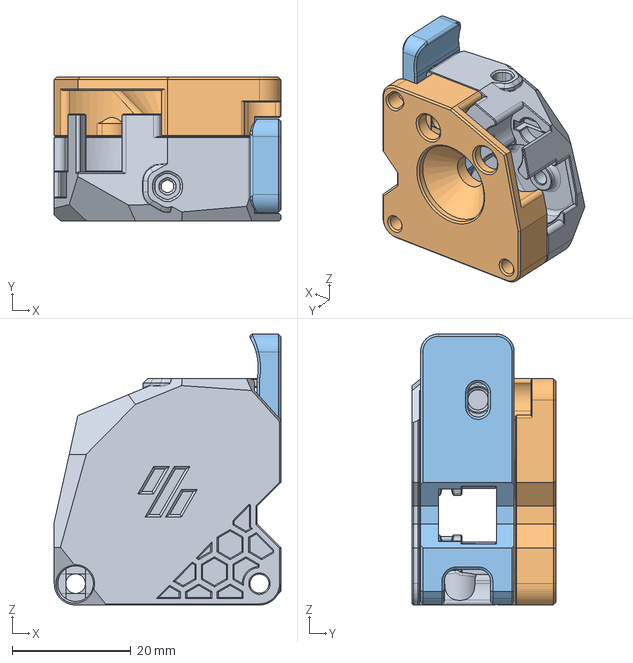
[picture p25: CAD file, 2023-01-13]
Extruders/Hummingbird/CAD/Hummingbird_extruder.step
38.2 x 24.2 x 45.7 mm

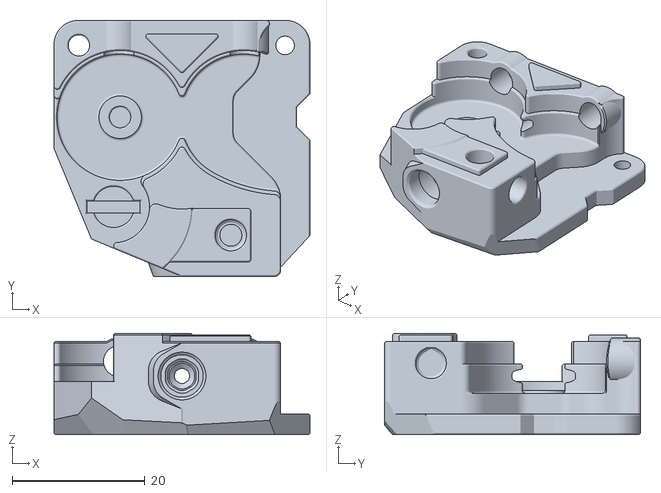
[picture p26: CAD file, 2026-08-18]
Extruders/Hummingbird_2.0/STLs/Front/Blank/Front_Collet_Blank.stl
38.5 x 38.5 x 15.2

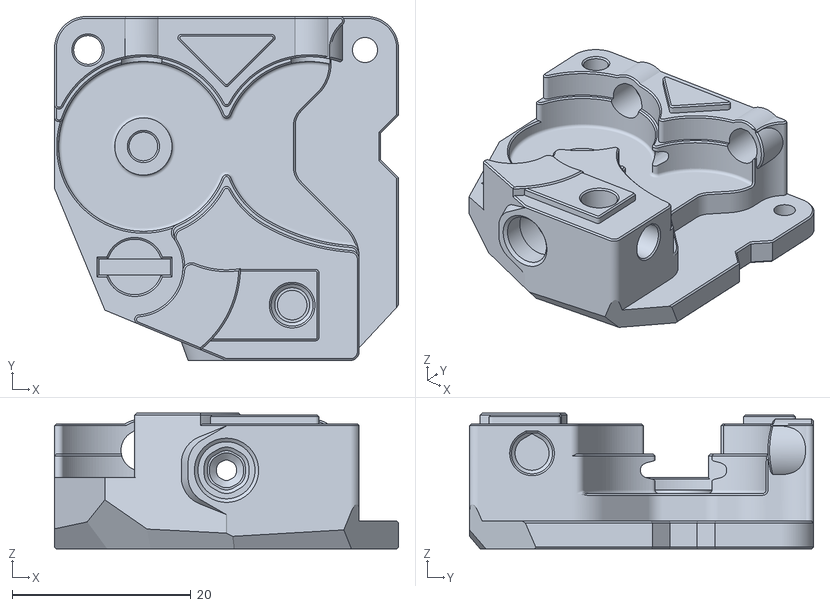
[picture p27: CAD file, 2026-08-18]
Extruders/Hummingbird_2.0/STLs/Front/Hummingbird_MMU/Front_Collet_Hummingbird_MMU.stl
38.5 x 38.5 x 15.2

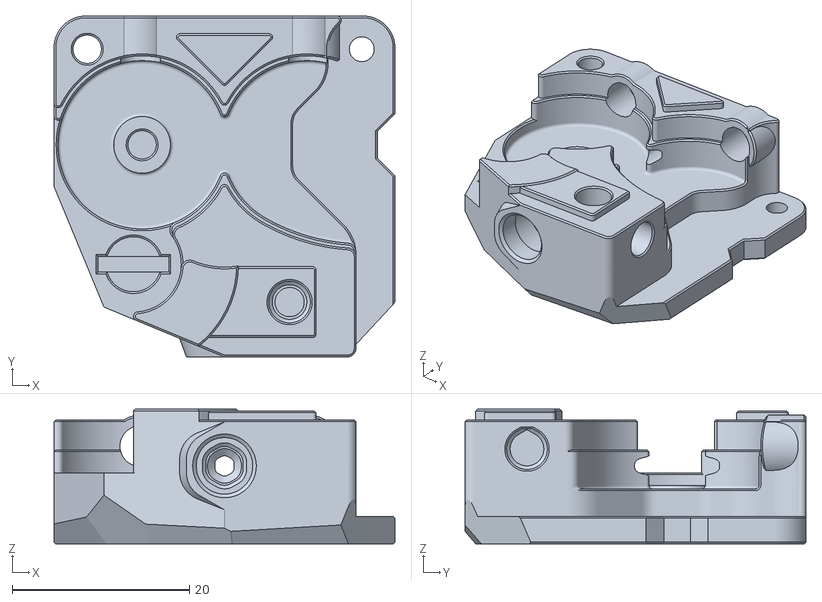
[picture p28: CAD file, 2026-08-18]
Extruders/Hummingbird_2.0/STLs/Front/Voron_MMU/Front_Collet_Voron_MMU.stl
38.5 x 38.5 x 15.2

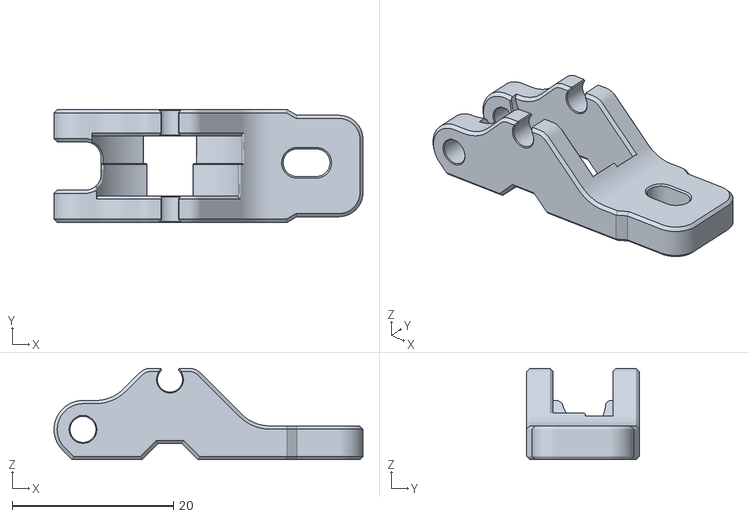
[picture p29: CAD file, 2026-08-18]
Extruders/Hummingbird_2.0/STLs/Idler_Arm_short.stl
38.3 x 14.0 x 11.4

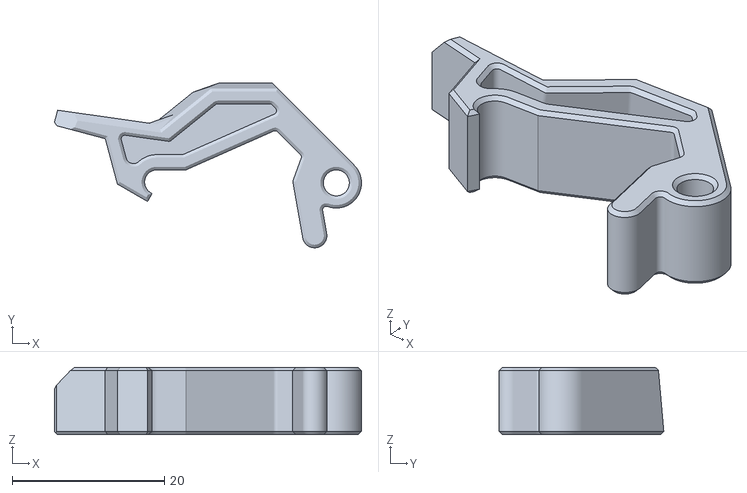
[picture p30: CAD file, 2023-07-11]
Extruders/Large_Gear_Clockwork2/STLs/[a]_latch.stl
40.3 x 21.6 x 8.80

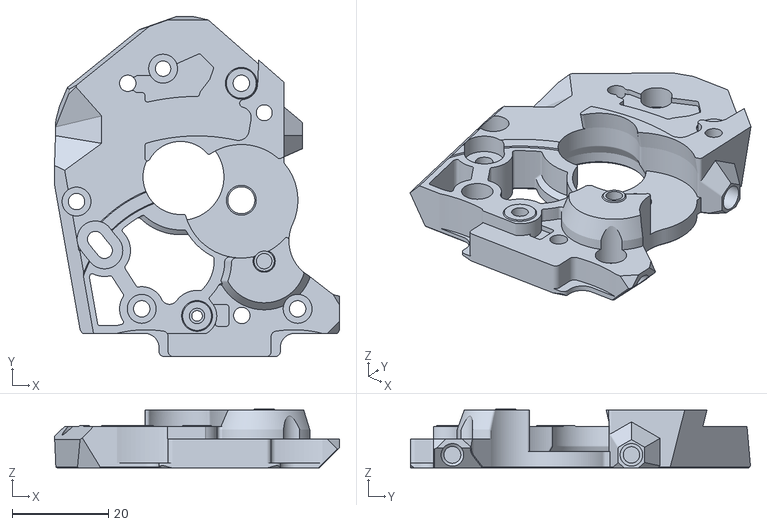
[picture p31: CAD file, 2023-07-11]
Extruders/Large_Gear_Clockwork2/STLs/HGX Lite gears/motor_plate_a-HGX.stl
59.2 x 70.6 x 12.2

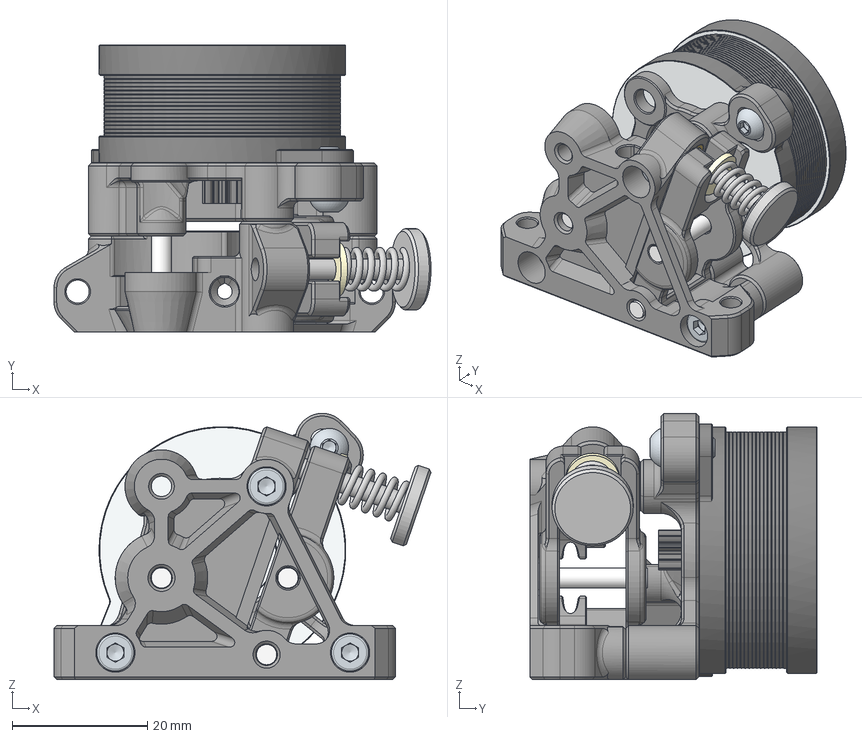
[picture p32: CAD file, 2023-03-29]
Extruders/ProtoXtruder/CAD/ProtoXtruder_LGX_gears.step
55.8 x 42.5 x 39.4 mm
Nylon Washer (Thumbscrew)
3mm shaft (16mm) x 2
Hex socket head cap screw M3x0.50 x 20 x 2
Hex socket head cap screw M3x0.50 x 16
Socket button head screw M3x0.5 x 8
Idler_arm
3mm shaft (24mm)
Back
Heat-Set Insert x 3
M3 Thumb Screw (1) (1)
Front
NEMA14_10t^sherpa_mini_a3_r9c

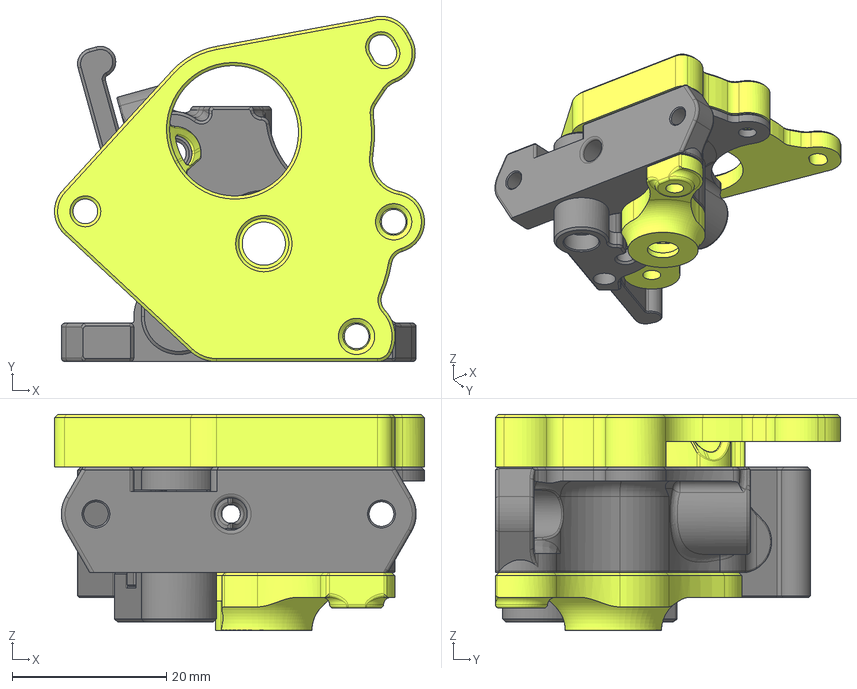
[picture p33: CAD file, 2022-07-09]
Extruders/Vorxtrudort/CAD/Vorxtrudort_OrbiterV2_FrictionFit.step
48.0 x 44.8 x 28.0 mm

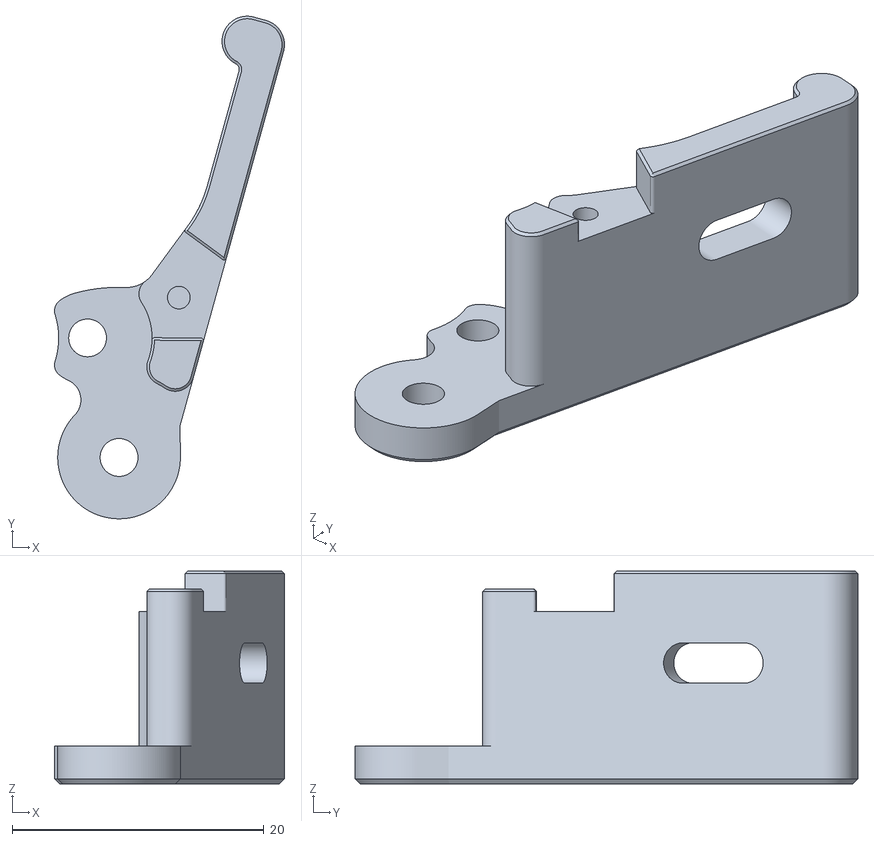
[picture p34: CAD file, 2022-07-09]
Extruders/Vorxtrudort/STLs/Tensioner_a.stl
18.3 x 39.9 x 16.9

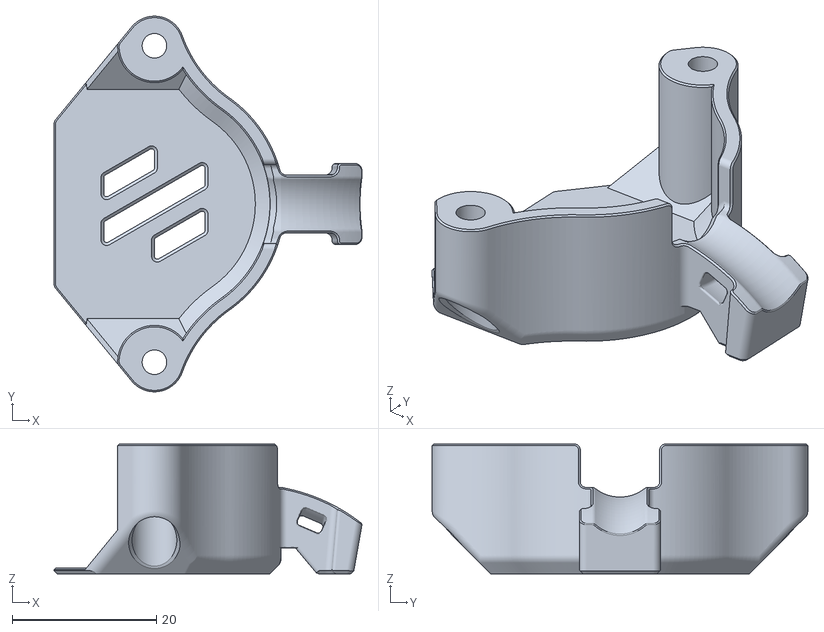
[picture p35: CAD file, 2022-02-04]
V0/Connector_cover/STL/Strain_Relief_Connector_Cover_x1.stl
42.7 x 52.0 x 18.0

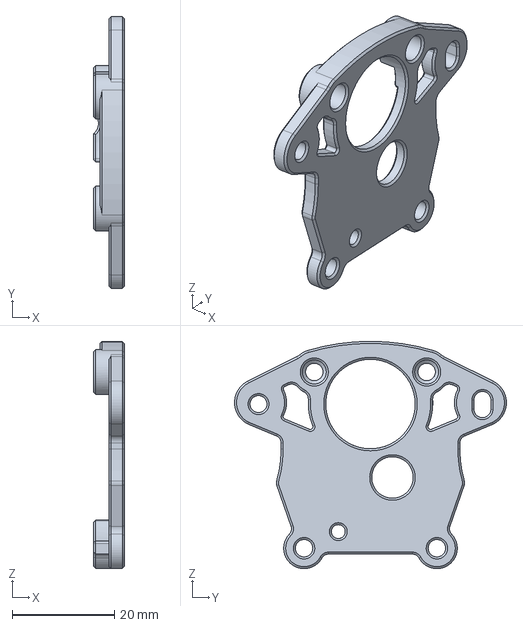
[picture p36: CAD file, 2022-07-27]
V0/Mini_afterburner_motor_frame/Motor_Frame.step
6.00 x 53.2 x 44.5 mm

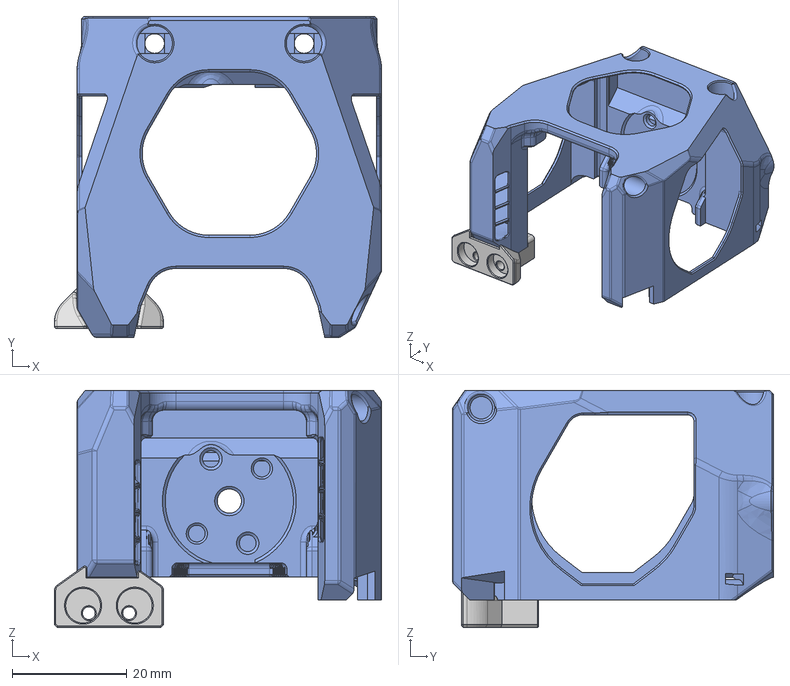
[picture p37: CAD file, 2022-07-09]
V0/Toolhead/CAD/Cowling.step
57.0 x 55.9 x 41.2 mm

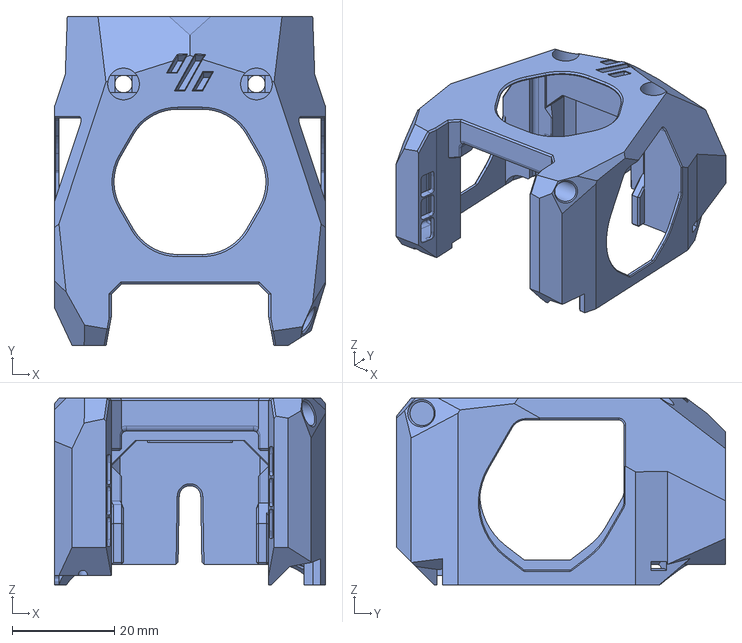
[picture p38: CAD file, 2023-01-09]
V0/Toolhead/CAD/Extruder_Adapters/Orbiter_V2_cowling.step
53.0 x 64.4 x 36.5 mm

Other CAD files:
Extruders/Hummingbird_2.0/STLs/Front/Hummingbird/Front_Collet_Hummingbird.stl
Extruders/Hummingbird_2.0/STLs/Front/Voron/Front_Collet_Voron.stl
Extruders/Large_Gear_Clockwork2/STLs/LGX Lite gears/motor_plate_a-LGX.stl
V0/Toolhead/STLs/ADXL345_Mount.stl
Extruders/Hummingbird/STLs/Back.stl
Extruders/Hummingbird/STLs/Idler_arm.stl
Extruders/Hummingbird/STLs/Idler_arm_short.stl
Extruders/Hummingbird_2.0/STLs/Back.stl
Extruders/Hummingbird_2.0/STLs/Front/Blank/Front_Blank.stl
Extruders/Hummingbird_2.0/STLs/Front/Blank/Front_ECAS04_Blank.stl
Extruders/Hummingbird_2.0/STLs/Front/Hummingbird/Front_ECAS04_Hummingbird.stl
Extruders/Hummingbird_2.0/STLs/Front/Hummingbird/Front_Hummingbird.stl
Extruders/Hummingbird_2.0/STLs/Front/Hummingbird_MMU/Front_ECAS04_Hummingbird_MMU.stl
Extruders/Hummingbird_2.0/STLs/Front/Hummingbird_MMU/Front_Hummingbird_MMU.stl
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

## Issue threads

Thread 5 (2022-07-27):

Missing STL

retsamedoc, 2022-07-27:
Missing STL in mini afterburner motor frame mod.

nhchiu, 2022-07-27:
Thanks a lot again for catching it!

If you gave it a try and you don't mind, any feedback would be appreciated.
Wonder if it really helps or is just useless. Thanks!

Closed 2022-07-27.

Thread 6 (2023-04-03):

LGX Version

scheini79, 2023-04-03:
Not really an issue, but wanted to confirm that LGX version is working as intended. Very good fitment.

nhchiu, 2023-04-08:
I'm sorry for the late reply.
May I ask which extruder did you try? I guess ProtoXtruder or CW2?
Sorry, they're all in the same repository so I'm not sure which one you are referring to.

But thank you very much for sharing your feedback. Much appreciated!

Closed 2023-05-21.

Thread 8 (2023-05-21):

This is not an issue but a question about the ProtoXtruder

erlis, 2023-05-21:
Why would the Klipper config be different from the settings I have with the lgx lite?

I'm considering reusing an old lgx lite I have around and use it's internal to use this protoXtruder with my mantis xol,  and see what results I'll get...

nhchiu, 2023-05-21:
Sorry, I don't have a Bondtech LGX lite.

erlis, 2023-05-21:
can you add a source for the 16mm shaft? I'm still searching and I can't find it yet... were did you get yours? Preferably in the US so I don't have to wait that long

nhchiu, 2023-05-22:
>  find it yet... were did you get yours? Preferably in the US so I don't have to wait that long

It is included in the HGX lite gear kit.

erlis, 2023-05-22:
> > find it yet... were did you get yours? Preferably in the US so I don't have to wait that long
>
> It is included in the HGX lite gear kit. If you are using the gears of LGX lite, you can probably reuse the shafts in it too.

Thanks, will look into it, I wasn't sure the shafts on the LGX Lite will be the same.

Closed 2023-06-27.

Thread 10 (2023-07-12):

sbb Can board

ITTV-tools, 2023-07-12:
could you please create a version for of the Large Gear Clockwork for the ebb2240 ?
https://github.com/bigtreetech/EBB/blob/master/EBB%20SB2240_2209%20CAN/Custom%20Printed%20Parts/main_body_EBB_SB.stl

appleimperio, 2023-08-11:
This would be great!

Zephyrus67, 2023-11-19:
I doubt that will be possible. The EBB 2240/2209 boards are too high and will conflict with one of the gears in the extruder. And moving the 2 gripping gears will most likely not be possible due to the path for the filament.

But lets see what the authot comes up with.

The alternative could be to use EBB36 CAN (for name 14) or EBB42 CAN (for nema 17) along with a hartk 2 piece PCB board.

nhchiu, 2023-11-19:
Sorry, somehow I missed this topic.

As @Zephyrus67 said, the EBB 2240/2209 board is too large and will interfere the lower gear.
Unfortunately I haven't found out an arrangement to make it fit without making major modifications like making the SB front cover wider or things like that. I'd like to keep the footprint as close to the stock CW2 as possible.

Closed 2023-11-23.

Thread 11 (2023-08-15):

Filament sensor for multicolor printing

deflord, 2023-08-15:
Hi!
Super work, thank you!
I want use your head with multicolor print system [EnragedRabbitProject](https://github.com/EtteGit/EnragedRabbitProject)
you can added microswitch or hall effect sensor to find filament?

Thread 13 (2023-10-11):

Standalone Sherpa-like version for Dragon Burner and the like?

viesturz, 2023-10-11:
Would be great if you can adapt this for standalone mounting on [Dragon burner](https://github.com/chirpy2605/voron) and friends.

viesturz, 2023-10-11:
Modifying the Hummingbird should be doable, trying that out...

viesturz, 2023-10-11:
And it's actually a thing, man you are awesome. A better front page listing all the projects would have been helpful, cheers!

Closed 2023-10-11.

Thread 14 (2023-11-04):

ProtoXtruder depth

GijsvanDulmen, 2023-11-04:
Thanks for the lovely extruder! Running it right now and was wondering about a few design decisions. It seems the extruder could become even less in depth by moving the large gear which transfer to the other two a bit to the front as well. So it picks up the two gears in the middle of the large gear instead of all the way at the end.

So I was wondering why you didn't opted for a less depth version of the ProtoXtruder. My toolhead is tiny and a few mm's less would even make it a better candidate for this toolhead (K3).

nhchiu, 2023-11-05:
> Thanks for the lovely extruder! Running it right now and was wondering about a few design decisions. It seems the extruder could become even less in depth by moving the large gear which transfer to the other two a bit to the front as well. So it picks up the two gears in the middle of the large gear instead of all the way at the end.
>
> So I was wondering why you didn't opted for a less depth version of the ProtoXtruder. My toolhead is tiny and a few mm's less would even make it a better candidate for this toolhead (K3).

Hello! Thanks for your question. It's because the front metal part of the extrusion gear is about half way the depth of the teeth bellow. So if the large gear moves any forward, the metal part will block the gears from meshing together.

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

Hope the screenshots explain what I was trying to say.

GijsvanDulmen, 2023-11-05:
Thanks for the info @nhchiu ! That was less obvious then expected ;-)

Too bad.. cause it would really help the extruder become less in depth. Hope there will be other gears in the future which skip that little piece of "nothing".

nhchiu, 2023-11-05:
> Thanks for the info @nhchiu ! That was less obvious then expected ;-)
>
> Too bad.. cause it would really help the extruder become less in depth. Hope there will be other gears in the future which skip that little piece of "nothing".

Yeah I want to get rid of the unnecessary extra depth too.
But, don't feel bad cause Haldis, the company making the HGX gears, has made a new version with slimmer gears and some other tweaks.
Currently there's no gear kit available but you can see the extruder they have here:
https://hs3dprinter.com/products/hgx

Closed 2023-11-05.

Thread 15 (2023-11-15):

[Question] Are any of the standard CW2 parts compatible with the Large Gear CW2 assembly?

tehniemer, 2023-11-15:
Like the title states, I'm wondering if I can use any of my existing CW2 parts, like the latch, latch shuttle, cable cover, and chain anchor with your version or if they differ from the original version files?

nhchiu, 2023-11-15:
> Like the title states, I'm wondering if I can use any of my existing CW2 parts, like the latch, latch shuttle, cable cover, and chain anchor with your version or if they differ from the original version files?

Hello. Unfortunately none of them are the same as the stock CW2 part.

Closed 2023-11-15.

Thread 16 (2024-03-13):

Large Gear Clockworks2 PTFE tube loosening

ArdaFu, 2024-03-13:
Hi,

The wall between the main body PTFE tube interface and the latch contact surface is too thin(1mm difference compare with std clockworks2), which leads to PTFE loosening after some time usage. Can you increase the thickness of this part?

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

ArdaFu, 2024-03-13:
maybe modify it like this.
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

nhchiu, 2024-03-14:
@ArdaFu Thanks for your suggestion. I'll try to fix that when I get time to work on it.

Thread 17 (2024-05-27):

Can you use LGX-lite gears

Plum6767, 2024-05-27:
Hello,

is it possible to reuse the internals of an lgx-lite, rather than purchase a hgx set?

nhchiu, 2024-05-28:
Hello. Which mod are you referring to?

Plum6767, 2024-05-28:
The Hummingbird extruder

nhchiu, 2024-05-28:
Sorry I didn't make a version for LGX lite gears as it is basically the same footprint as LGX lite.

Closed 2024-05-31.

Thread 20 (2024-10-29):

Improved bite depth and reliability by considering idler arm flexibility.

MartijnGevaert, 2024-10-29:
The geometry of Protoxtruder is spot on, where if the idler sits flush against the extruder body, the bite depth should be sufficient for any use case.
However, due to the nature of plastic parts, the idler arm itself flexes a bit when filament is inserted.
This means that even when filament is inserted, the top of the idler arm can be pushed flush against the extruder body at the top of the extruder, while the bite depth is still insufficient. The idler simply "flexes" out of the way.
Therefore the bite depth ends up being regulated by the force required to deform the idler arm, not the force created by the spring.
This means the protoxtruder is essentially running a fixed idler, the spring never compresses.
The immediate downside of this is that this limits the max amount of bite force.

The arrows in the image below show the forces at work.
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

# solution 1
The first solution I came up with, is to modify the extruder so that idler arm does not touch the extruder when filament is inserted and the screw is tensioned to your liking. This will also ensure, that over time, if the idler arm starts to bend a bit, there's still enough travel on the arm to ensure proper bite force.

I have already partially achieved this by removing some material from the idler arm as shown in the image below. Allowing about 1mm more travel on the top of the arm. The idler arm still sits flush with the extruder at the top, but now grip is much better.
While before occasional filament slippage would occur, now the stepper motor skips instead, showing that the grip on the filament is no longer the limiting factor.

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

### Downsides
This does make the extruder a bit less fool proof. It's now easier for the idler to be over-tensioned and for bite depth to be too deep.

# Solution 2
Simply getting rid of the flex in the idler arm. Beefing up the idler arm will reduce flex, while still not allowing bite depths that are too deep. Although there will still always be some flex.

### Downsides
Can't think of any

# Conclusion
The least amount of work might be a combination of solution 1 and 2, removing some material on the idler allowing for more travel, and adding some material on the outside to reduce flex.

Let me know if there's anything more I can do!

nhchiu, 2024-10-30:
Hello! First of all, thanks for your finding and investigation.

I hope this question doesn't come as offensive. Have you seen this issue happening?
I'm asking because I haven't heard feedback with this issue, not trying to deny it.

Regarding your solution 1, the design already kind of have this solution built in. (Admittedly it might not be enough).
This is what I expect to happen. The gap between the idler and main body is larger than the clearance needed for printed parts. When no filament is inserted, the idler arm will "eat up" the gap at the top. Now the two drive gears are closer to each other and the gap between the grooves should be narrower than the filament diameter.
When the filament is inserted, it pushes the idler arm outwards and now the idler arm should be back to the rest position in CAD, or even slightly more "open".

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

What I'm trying to show here is that there is some room for the idler arm to bend before it cannot apply biting force on the filament.
But depending on the size and strength of the printed parts, the actual diameter of the filament, and even the softness of the material, the required gap in design can vary, so it might need more tweaking to work in most cases.

The reason why I don't just leave a much larger gap in there is that people often over-tension the idler, and the excessive force can cause other issues. For example, squeezing the filament too hard and deform the filament (especially when printing TPU), twisting the dual drive gears and causing bad gear contact, or causing permanent bending on the idler arm.

I can try to increase the space that the idler arm could bend and also try to beef up the printed parts if you are having this issue.
Thank you!

MartijnGevaert, 2024-11-04:
Of course your question isn't offensive! I get you need to check against common user error and such.

Yes, I was seeing this issue. I was getting insufficient filament bite, what I was seeing is that the filament slipped, instead of the stepper motor skipping in scenario's where flow rate limits where being hit.
This same stepper motors does skip when combined with RIDGA bmg gears instead of the gears slipping. This indicates that filament grip was lower than achieved with BMG gears (sherpa mini), despite the drive wheels being larger.
Running at these very high flow rate speeds doesn't make all too much sense, since filament ends up being not molten, but it becomes relevant again when dealing with large spools (5kg) or when that little bit more force can push through a filament clog on it's own and prevent a failed print.

The current design does prevent overtensioning, but unfortunately does not account for the flex in the extruder arm.

The no-downsides improvement would indeed be to increase the idler arm stiffness. It should be possible, I do suspect doubling the thickness of the idler arm would not be overkill. Functionally not much of an issue I don't think, it might look a bit funny though.
This could solve the idler arm flex issue, without allowing the possibility of over-tensioning.
That being said, there's very little room for flex, or idler deformation over time in the current design.

Alternatively, one could also only make room where I marked green on the image below. That way the bite depth is still limited, but the idler arm flex is accounted for.
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

nhchiu, 2024-11-21:
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

Sorry for the late reply.

I guess it's caused by the update made in Aug.

I'll make a quick hotfix before I can make a overall fix for the flex in the idler arm.

Thank you for the feedback and suggestion.

MartijnGevaert, 2024-11-21:
I did further notice the issue doesn't occur with PETG (softer) but it does occur with ABS/ASA (harder) which I suspect need more force for good bite depth. This slightly further confirmes the idler arm flex theory... I think.... your idea of beefing up the idler arm seems the best initial fix to try.

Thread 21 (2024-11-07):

Large Gear Clockworks2 HGX lite gear wheel aligning

richard9999999999, 2024-11-07:
Hello, I have built HGX lite version and noticed a following problem:
The middle gear has axial play about 1mm. Yes, it doesn't need to be a problem however I see that:
- when the middle gear is in a position nearest to the stepper, the stepper's gear still isn't engaged in its full thickness to the middle gear. Plus in this position the middle gear and extruding gears are not fully engaged (in thickness)
- when the middle gear is in position nearest to the part cooling fan, the stepper's gear is engaged 1mm less than in the above case
The steppers have specified 6mm from the base plate to top of gear wheel (mine has 6.5mm) so it seems your extruder's base plate is just too thick..

I modified "motor_plate_a-HGX" for my the test purpose: I made the base plate (where stepper is mounted) 1mm thinner plus I made the cutout for the middle wheel 0.8mm less deep and also shifted the seat for middle gear bearing 0.8mm away from the stepper. Plus of course I had to do make "motor_plate_b" 1mm thicker..
Plus after this my mode there is a problem with heatset inserts (both for PCB) which also need to be shifted 1mm (besides I suppose this way they will receive more contact distance when plugged in): I have made that by forcing them in appropriate direction while seating of inserts and filling the created gaps using CA glue.

I also noticed that step CAD file doesn't contain correct bearing seat for HGX in motor_plate_a I suppose it is LGX version file? If yes, please could you share also HGX CAD file?

Thanks,
Richard

nhchiu, 2024-11-07:
1. Yes the gears aren't designed to be fully overlapping depth-wise. That's a trade off of taking the length of screws, the filament path, position of heatset inserts, and so on, into consideration and not to causing interference or having super thin walls.

2. The positions of the PCB mounting inserts should be matching those on the stock CW2. But feel free to modify it to make a better fit for the PCB you have.

3. Both the HGX and LGX parts are included in the STEP file and the parts are named accordingly.

richard9999999999, 2024-11-07:
1) The stepper gear is 4mm wide. You arrangement makes floating of gear overlaping somewhere between 3.5mm and 2.5mm.. I think 2.5mm overlapping from 4mm plastic/metal gear contact doesn't sound great in term of function/longevity, that's the reason I tried to solve it in my case. However I may be wrong..

I have made just quick and simple mod which tries to solve the problem while maintaining the same screws and filament path. Heatset inserts can be solved also (which I didn't chose to do in the model). Yes, the back plate is 1mm thinner than your original in the thickest place but it is the same thicknesses in the thinnest place and it is much more thick/robust than CW2 motor plate..

2. OK, I mentioned PCB holding inserts just because my "quick ans simple" mod makes the rear one partly in air.. It is doable however. When you mention that the inserts maintain CW2 position I suppose you meant just position in the axle parallel to stepper axle and in vertical axle. In horizontal axle the position is shifted some milimeters to right (when viewing to stealthbutner from front). It is due to larger dimensions of the gear mechanize I suppose..

3. I found that now, thank you

BTW thank you for your work, I appreciate it.

nhchiu, 2024-11-07:
> 1. The stepper gear is 4mm wide. You arrangement makes floating of gear overlapping somewhere between 3.5mm and 2.5mm.. I think 2.5mm overlapping from 4mm plastic/metal gear contact doesn't sound great in term of function/longevity, that's the reason I tried to solve it in my case. However I may be wrong..
>
> I have made just quick and simple mod which tries to solve the problem while maintaining the same screws and filament path. Heatset inserts can be solved also (which I didn't chose to do in the model). Yes, the back plate is 1mm thinner than your original in the thickest place but it has the same thickness in the thinnest place and it is much more thick/robust than CW2 motor plate..

I agree. It's not ideal and I don't like it either. But I haven't got time to fix it yet.

> 2. OK, I mentioned PCB holding inserts just because my "quick and simple" mod makes the rear one partly in air.. It is doable however. When you mention that the inserts maintain CW2 position I suppose you meant just position in the axle parallel to stepper axle and in vertical axle. In horizontal axle the position is shifted some millimeters to right (when viewing to stealthbutner from front). It is due to larger dimensions of the gear mechanism I suppose..

No I mean the exact 3D position. The stock CW2 has a PCB spacer.

richard9999999999, 2024-11-07:
>>No I mean the exact 3D position. The stock CW2 has a PCB spacer.
OK. Still it is strange that even when I don't use spacer I have problem to fit my SB2040 board under the cover (I need to cut a heatsink a bit). However it is just a minor annoyance..

Thanks for answers.

Closed 2024-11-07.

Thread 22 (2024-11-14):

Hummingbird Extruder: Gears axial movements

fifonik, 2024-11-14:
Thanks a lot, the feeder looks very good and 3D printing friendly.

I've just printed it and see some axial movements on all gears (~0.5mm).
I compared it with anther model for the gears set from printables (I printed earlier) and noticed that the gap is slightly smaller there (~0.3mm, measured in slicer), so there is almost no such axial gears movement.
Am I supposed to use some washers with this model?

Thanks.

fifonik, 2024-11-14:
Ah, sorry. I thought this git is for one extruder.
I'm talking about Hummingbird

nhchiu, 2024-11-14:
> Ah, sorry. I thought this git is for one extruder only (followed the link from printables and then clicked 'Issues'). I'm talking about Hummingbird (added extruder in the ticket's title)

No problem. Then the gap is fine.
I left it a bit wider due to possible errors in the measurements I've done. In next update I will tweak it to have a smaller gap (to the same as the ProtoXtruder). But it should work fine as it is now.

Closed 2024-11-14.

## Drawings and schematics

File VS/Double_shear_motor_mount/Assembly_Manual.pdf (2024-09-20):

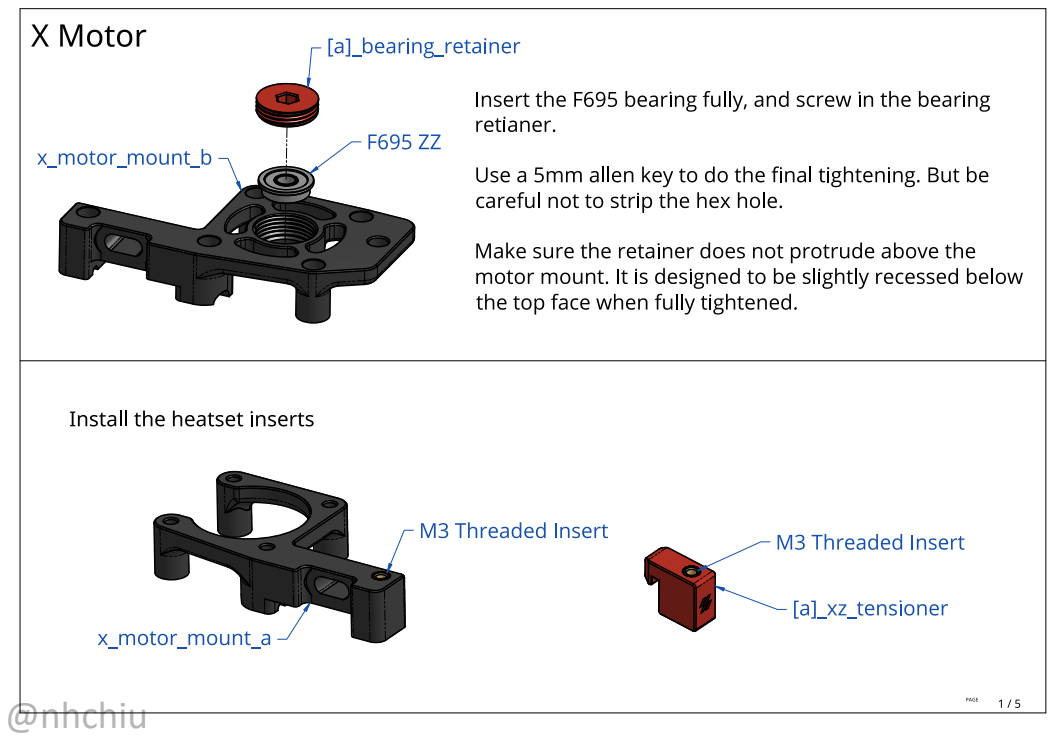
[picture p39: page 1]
@nhchiu

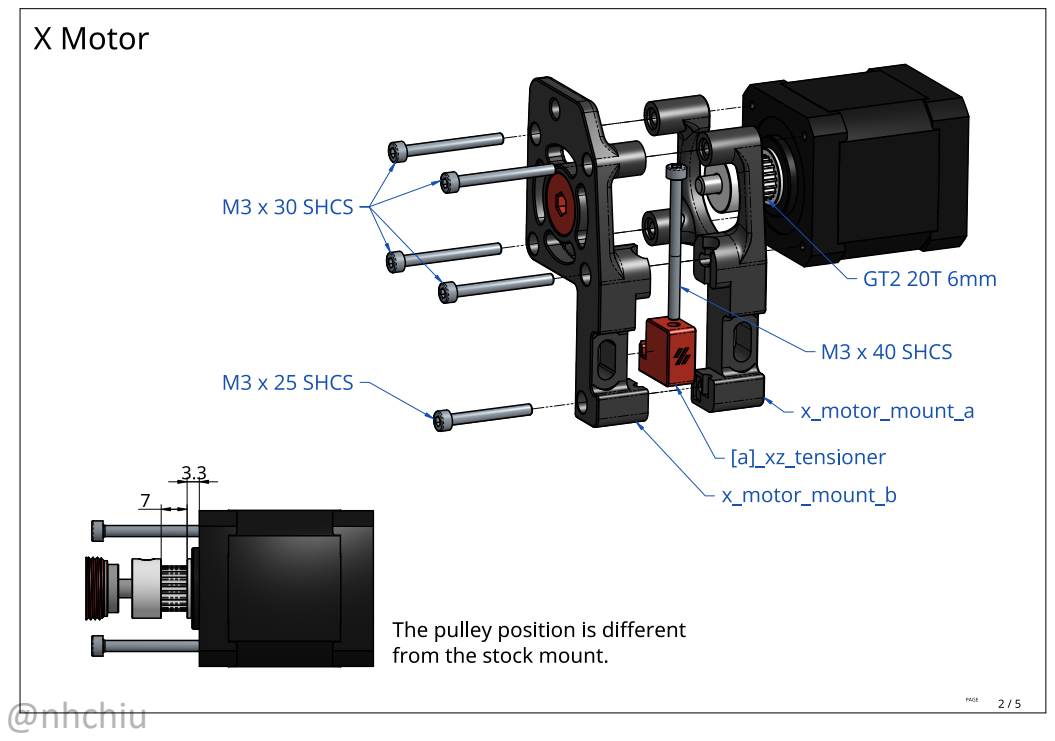
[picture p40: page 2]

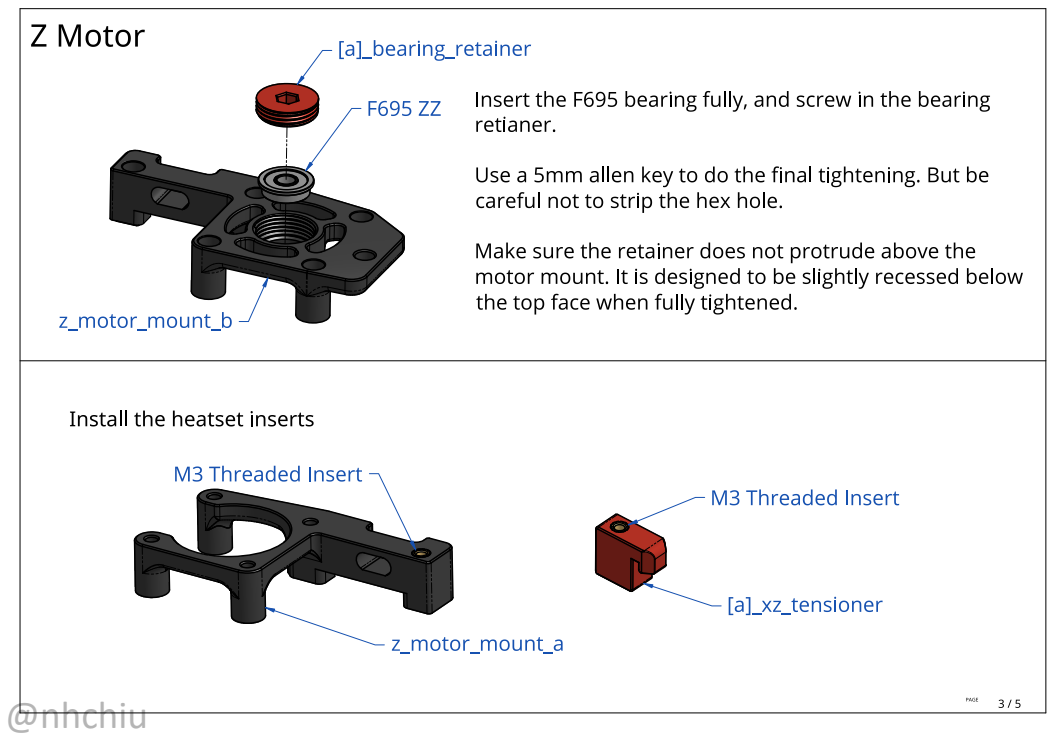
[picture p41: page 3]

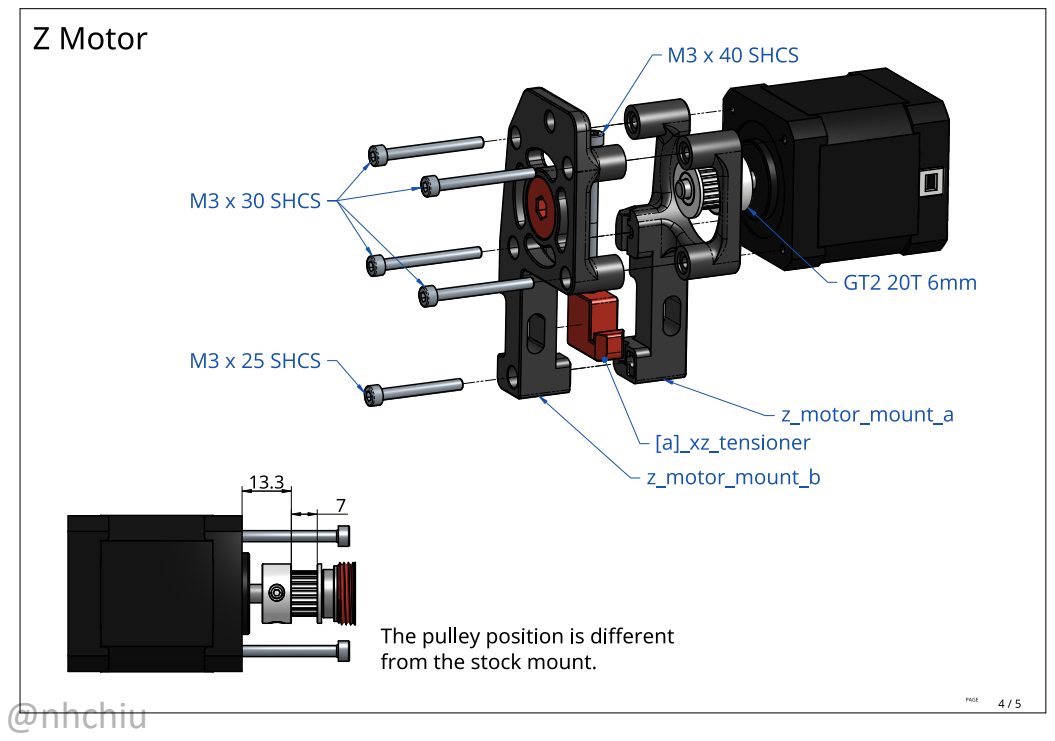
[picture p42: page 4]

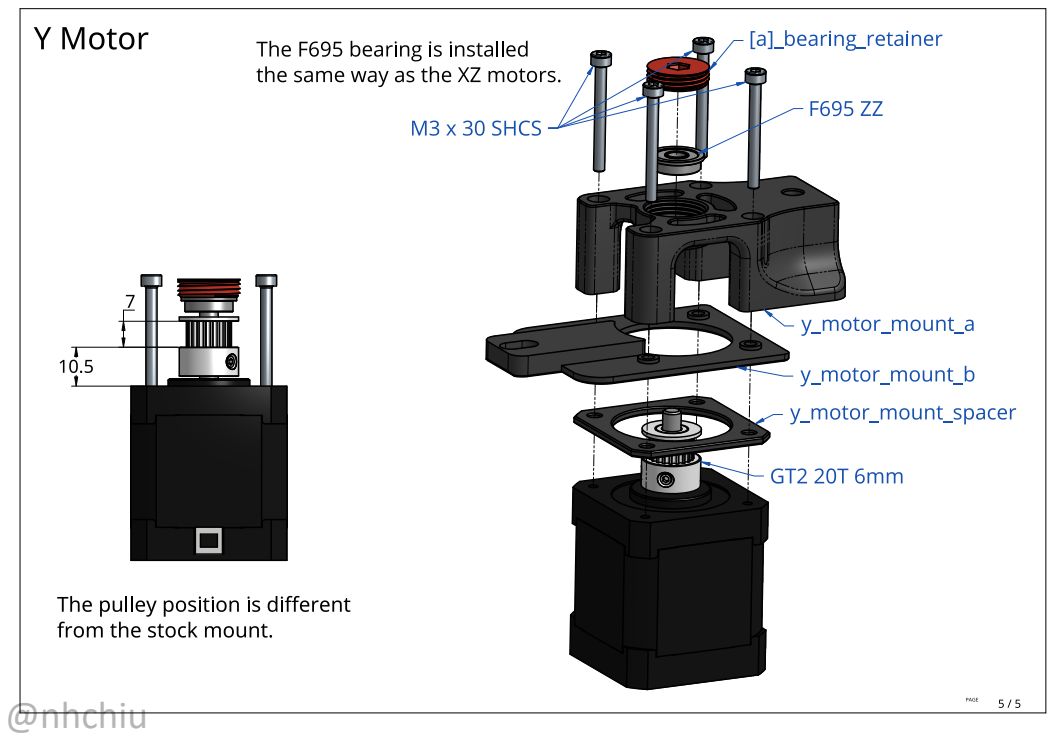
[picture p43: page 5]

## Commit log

2022-01-16 Add X-MGN9C mod
    [A_Drive_Frame_Lower_x1.stl, B_Drive_Frame_Lower_x1.stl, M3_Nut_Spacer_x1.stl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]
2022-01-16 [ImgBot] Optimize images
    *Total -- 308.17kb -> 232.86kb (24.44%)
    /V0/X_axis_MGN9C/Images/X_Carriage.png -- 97.58kb -> 46.04kb (52.82%)
    /V0/X_axis_MGN9C/Images/M3_Nut_Spacers.png -- 104.47kb -> 91.73kb (12.2%)
    /V0/X_axis_MGN9C/Images/Motor_Mount.png -- 106.12kb -> 95.10kb (10.38%)
2022-02-04 Add Connector Cover for V0.1
    [Strain_Relief_Connector_Cover_x1.stl]
2022-02-04 [ImgBot] Optimize images
    *Total -- 2,734.16kb -> 2,547.38kb (6.83%)
    /V0/Connector_cover/Images/Thumbnail.png -- 246.79kb -> 211.92kb (14.13%)
    /V0/Connector_cover/Images/Front_and_Side_View.png -- 115.74kb -> 104.67kb (9.56%)
    /V0/Connector_cover/Images/Messy_Connectors.jpg -- 589.57kb -> 550.84kb (6.57%)
    /V0/Connector_cover/Images/Front.jpg -- 626.39kb -> 587.18kb (6.26%)
    /V0/Connector_cover/Images/Cover.jpg -- 493.39kb -> 466.45kb (5.46%)
    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
2022-07-04 Add motor frame mod for mini-afterburner
2022-07-04 [ImgBot] Optimize images
    *Total -- 1,006.51kb -> 976.38kb (2.99%)
    /V0/Mini_afterburner_motor_frame/Images/motor_frame.png -- 232.89kb -> 208.46kb (10.49%)
    /V0/Mini_afterburner_motor_frame/Images/7.jpg -- 253.35kb -> 248.02kb (2.1%)
    /V0/Mini_afterburner_motor_frame/Images/4.jpg -- 198.61kb -> 198.25kb (0.18%)
    /V0/Mini_afterburner_motor_frame/Images/6.jpg -- 321.65kb -> 321.65kb (0%)
2022-07-09 Add Vorxtrudort
    [BackPlate.stl, FrontCover.stl, Tensioner_a.stl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]
2022-07-09 Add toolhead mod
    [Cowling.step, Zeroclick_Probe_Mod.stl]
2022-07-10 [ImgBot] Optimize images
    *Total -- 4,514.34kb -> 3,969.04kb (12.08%)
    /Extruder/Images/Mount.png -- 122.90kb -> 53.95kb (56.11%)
    /V0/Toolhead/Images/Drawing.png -- 140.38kb -> 96.69kb (31.12%)
    /Extruder/Images/Tensioner.png -- 81.76kb -> 63.11kb (22.8%)
    /Extruder/Images/MidBody.png -- 116.37kb -> 92.30kb (20.68%)
    /Extruder/Images/MainAssembly.png -- 304.76kb -> 242.26kb (20.51%)
    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
2022-07-16 Add E3D Revo Voron for toolhead mod
2022-07-27 Add stl and step files for miniAB motor frame
    Fixes #5.
    [Motor_Frame.step, Motor_Frame.stl]
2022-07-29 Update the V0 toolhead
    - Revised the fan duct
    - Moved the zip tie slot higher so it clears the X carriage
    - Tweaked some faces and removed most of the fillets
2022-08-03 Added untested support for Sailfin and OrbiterV1.5
    [4mm_spacer.step, 4mm_spacer.stl, Orbiter_V1.5_adapter.step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]
2022-10-20 Update README.md
    Added ko-fi support button!
2023-01-09 Update CAD and STL files for new version
    [4mm_spacer.step, 4mm_spacer.stl, ADXL345_Mount.stl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]
2023-01-13 Move files
    [BackPlate.stl, FrontCover.stl, Tensioner_a.stl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]
2023-01-13 Add Hummingbird extruder
    [Back.stl, Hummingbird_extruder.step, Tensioner_arm.stl]
2023-02-20 Add Large gear CW2
    [[a]_guidler_a.stl, [a]_guidler_b.stl, [a]_latch.stl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]
2023-02-20 Add notes about toolhead board with large gear CW2
2023-03-29 Add ProtoXtruder
    [Back.stl, Front.stl, Idler_arm.stl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]
2023-03-29 Remove the assembling video of ProtoXtruder
2023-03-31 Update hummingbird extruder
    [Back.stl, Idler_arm.stl, Idler_arm_short.stl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]
2023-04-05 Add new exploded view to Hummingbird extruder
2023-04-05 [ImgBot] Optimize images
    *Total -- 13,205.14kb -> 12,697.94kb (3.84%)
    /Extruders/Hummingbird/Images/Assembly.png -- 203.14kb -> 156.62kb (22.9%)
    /Extruders/ProtoXtruder/Images/Assembly.jpeg -- 395.49kb -> 308.34kb (22.04%)
    /Extruders/Hummingbird/Images/Assembly2.png -- 157.06kb -> 125.44kb (20.13%)
    /V0/Toolhead/Images/ADXL345.png -- 246.47kb -> 206.07kb (16.39%)
    /Extruders/ProtoXtruder/Images/Dimension.png -- 166.56kb -> 141.16kb (15.25%)
    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
2023-06-27 Add PTFE tube retainers to Hummingbird extruder
    [Back.stl, Idler_arm.stl, Idler_arm_short.stl]
2023-06-27 Add images for bowden tube retainers
2023-06-30 Update toolhead board compatibility explanation
2023-07-01 Fix PC4-M6 thread
2023-07-01 Fix MMU STL files
2023-07-03 Update ProtoXtruder
    [Back.stl, Idler_arm.stl]
2023-07-03 Update images for tube retainers
2023-07-03 [ImgBot] Optimize images
    *Total -- 2,169.65kb -> 1,899.46kb (12.45%)
    /Extruders/ProtoXtruder/Images/Assembly.jpeg -- 395.00kb -> 307.90kb (22.05%)
    /Extruders/Hummingbird/Images/Slicer.png -- 366.09kb -> 297.45kb (18.75%)
    /Extruders/Hummingbird/Images/retainers.png -- 237.65kb -> 211.74kb (10.9%)
    /Extruders/ProtoXtruder/Images/retainers.png -- 237.65kb -> 211.74kb (10.9%)
    /Extruders/Hummingbird/Images/photo3.jpg -- 610.82kb -> 569.28kb (6.8%)
    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
2023-07-11 Update large gear CW2
    [[a]_guidler_a.stl, [a]_guidler_b.stl, [a]_latch.stl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]
2024-05-08 Remove the mockup gears in CAD to avoid confusion
2024-07-31 [PX] New release
    [Back.stl, Idler_arm.stl]
2024-09-20 Add Switchwire double shear motor mount
    [Y Motor.step, [a]_bearing_retainer_x3.stl, [a]_xz_tensioner_x2.stl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]
2024-09-21 [VS motor mount] Add cross section view
2024-12-12 [PX] Address some issues
    [Back.stl, Idler_arm.stl]
2024-12-12 [PX] Update README about new gear kits
